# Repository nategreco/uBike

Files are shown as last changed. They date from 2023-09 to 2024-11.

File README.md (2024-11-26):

# Universal Bike Controller
The Universal Bike Controller is an open-source project aimed at providing a drop-in replacement for the factory console on NordicTrack® S-series exercise bikes (s10i, s15i, s22i, and s27i). This project allows you to upgrade and customize your bike's control system with new features and improvements.

## Explanation
The factory consoles on NordicTrack® S-series bikes may lack certain features or customization options that users desire. The Universal Bike Controller project addresses these limitations by providing an open-source solution that simplifies the hardware on the bike while unlocking connectivity to other third-party apps (Zwift®, Rouvy®, Peloton®) and smart devices.

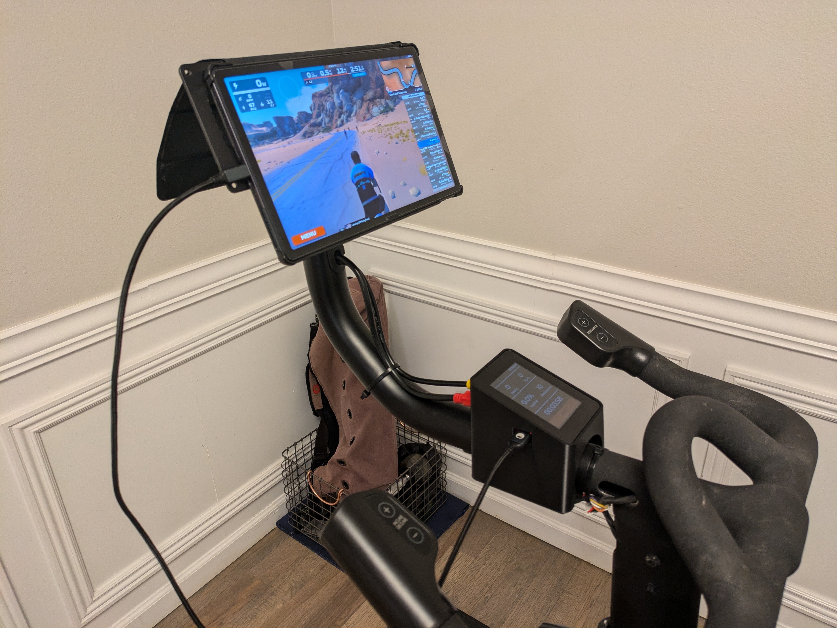
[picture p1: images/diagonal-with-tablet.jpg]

(Tablet not included)

## Features
- Drop-in replacement controller for the iFit console
  - **Note - This controller and the OEM console cannot be used together**
- Full incline and resistance control via OEM handlebar pushbuttons
- Wireless connectivity to a variety of third-party applications
- 3.5" TFT touchscreen for reseting elapsed time
- USB Type A fast charger port for charging
- Over-the-air support for future software upgrades

## Installation
The replacement uBike console mounts in the current location of the weight tray and plugs into the same two cables as the factory console. Installation is as simple as follows:
1. Turn off the bike
1. Remove the 4 screws from the underside of the weight tray (save them) and remove the weight tray
1. Place the uBike controller in its place, with the connectors facing away from the rider
1. Use the same 4 screws removed from the weight tray to secure the uBike controller
1. Unplug the 2 cables from the factory console and plug them into the new uBike controller
  * **Please see note below on compatability if you do not have a red and yellow connector**

## Compatibility
The Universal Bike Controller is designed to be compatible with the following NordicTrack® S-series exercise bikes:
- s10i
- s15i
- s22i
- s27i

All of these versions have been tested and are working.  Additionally, since 2021 bikes have stopped shipping with the yellow and red mini-DIN connectors to the console, instead they have cables coming directly out of the console.  **If your bike does not have the red and yellow connectors** you will need to buy the cables below:
* Yellow mini-DIN-6 Connector - PN 411540 ([eBay](https://www.ebay.com/itm/255061719835)/[HydraFitness](https://hydrafitnessparts.com/collections/stationary-bike-wires-and-wire-harness/products/nordictrack-comm-s22i-s15i-s10i-stationary-bike-upper-wire-harness-411540))
* Red mini-DIN-8 Connector - PN 411536 ([eBay](https://www.ebay.com/itm/265237954787)/[HydraFitness](https://hydrafitnessparts.com/collections/stationary-bike-wires-and-wire-harness/products/nordictrack-comm-s22i-s15i-s10i-stationary-bike-extension-wire-harness-4115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))

## Additional Reference Photos
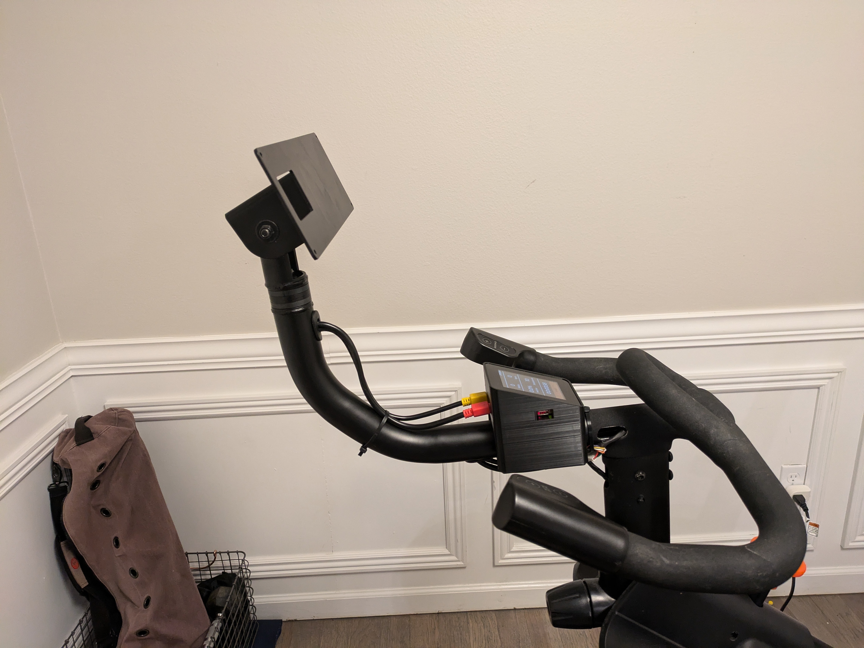
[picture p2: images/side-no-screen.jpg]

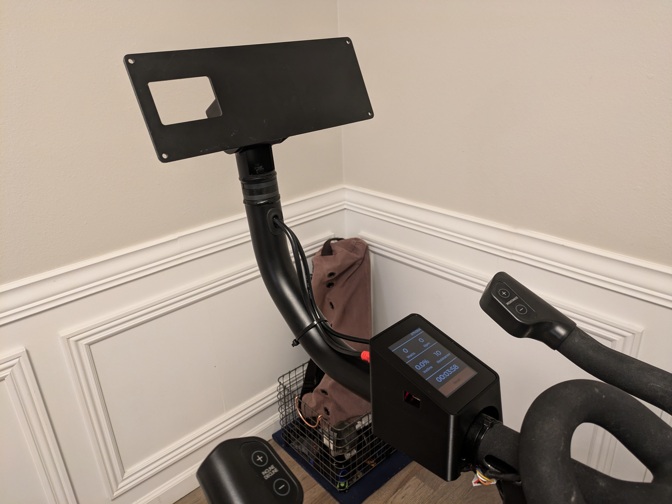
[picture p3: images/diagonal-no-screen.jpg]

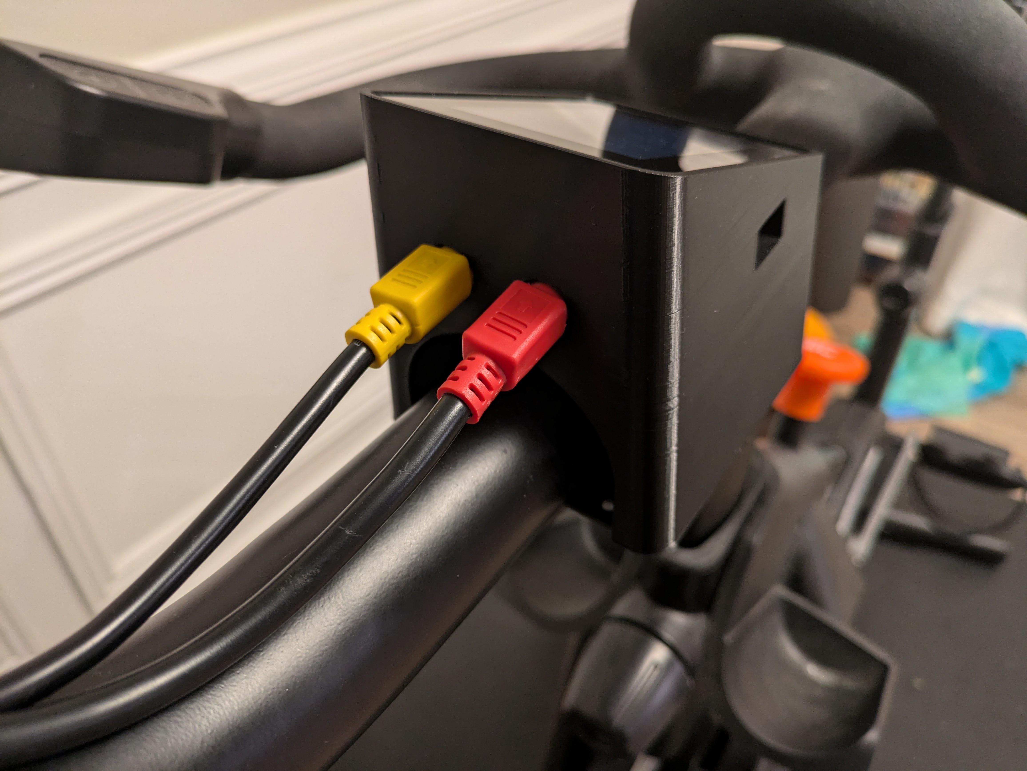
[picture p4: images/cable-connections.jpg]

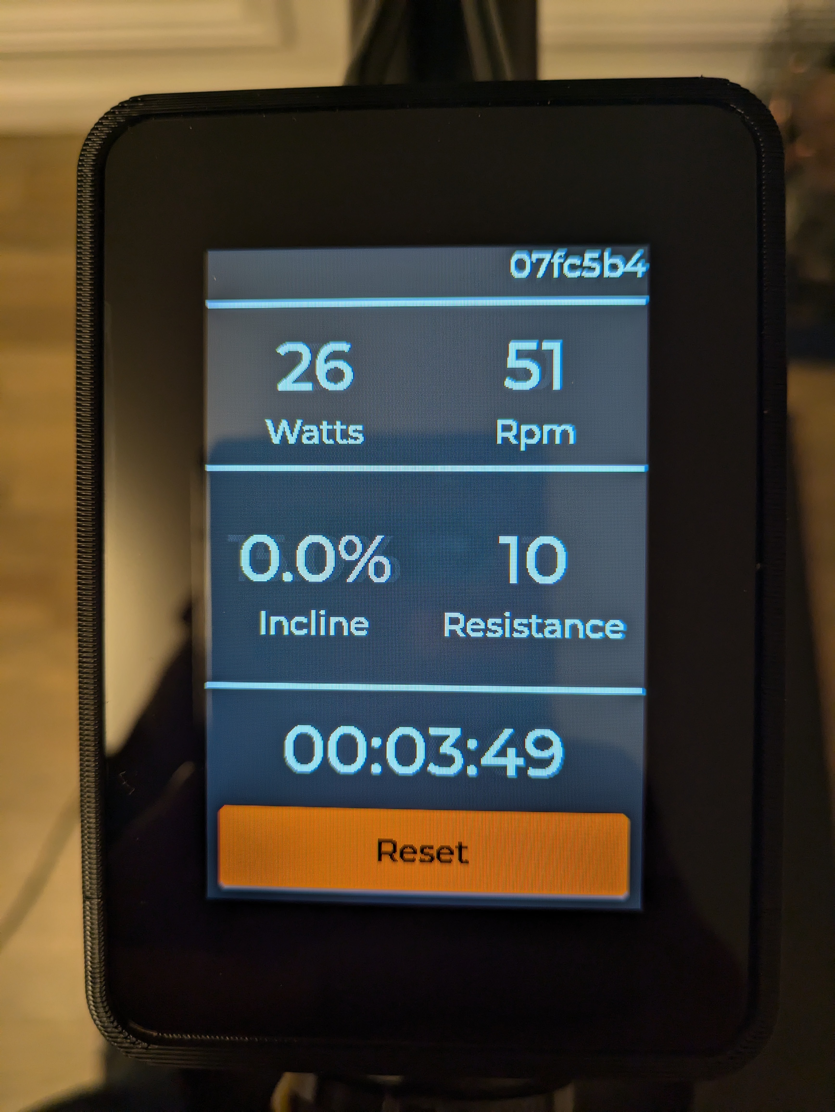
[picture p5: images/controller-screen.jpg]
Universal Bike Controller

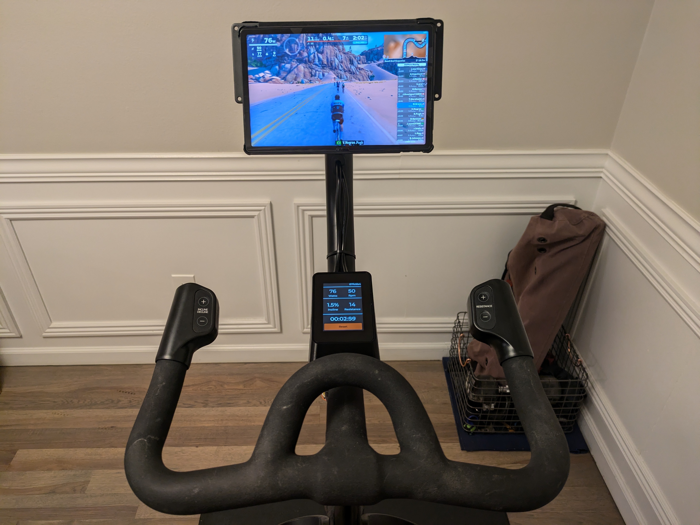
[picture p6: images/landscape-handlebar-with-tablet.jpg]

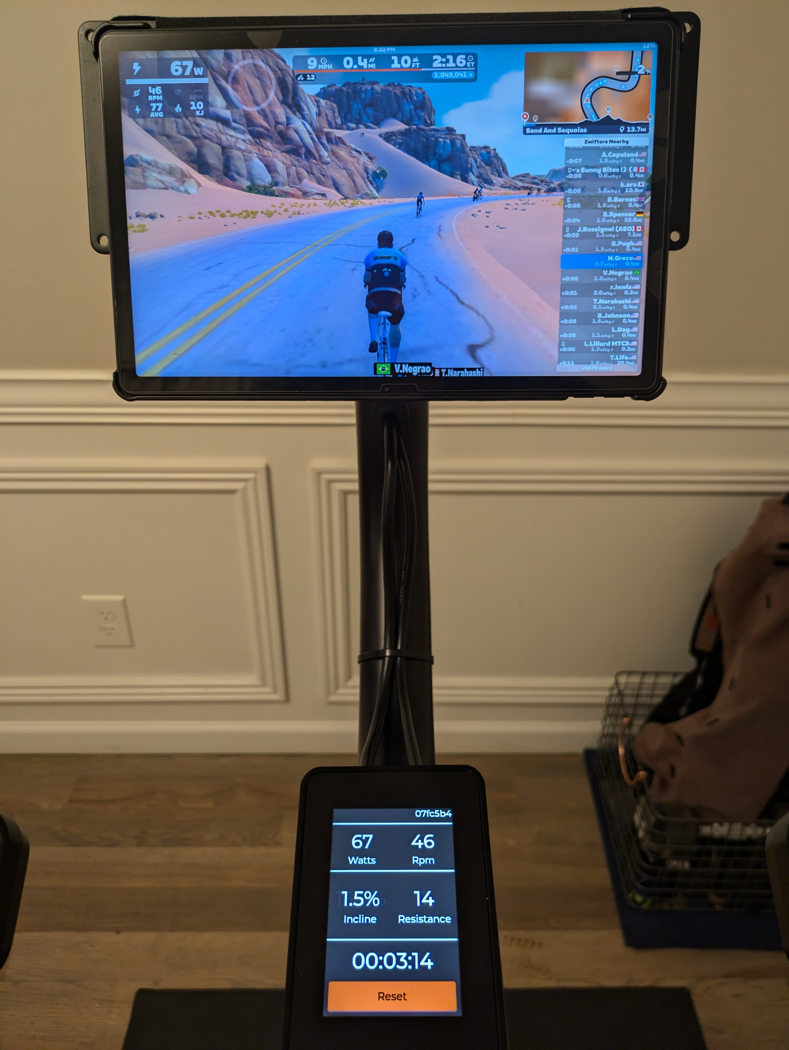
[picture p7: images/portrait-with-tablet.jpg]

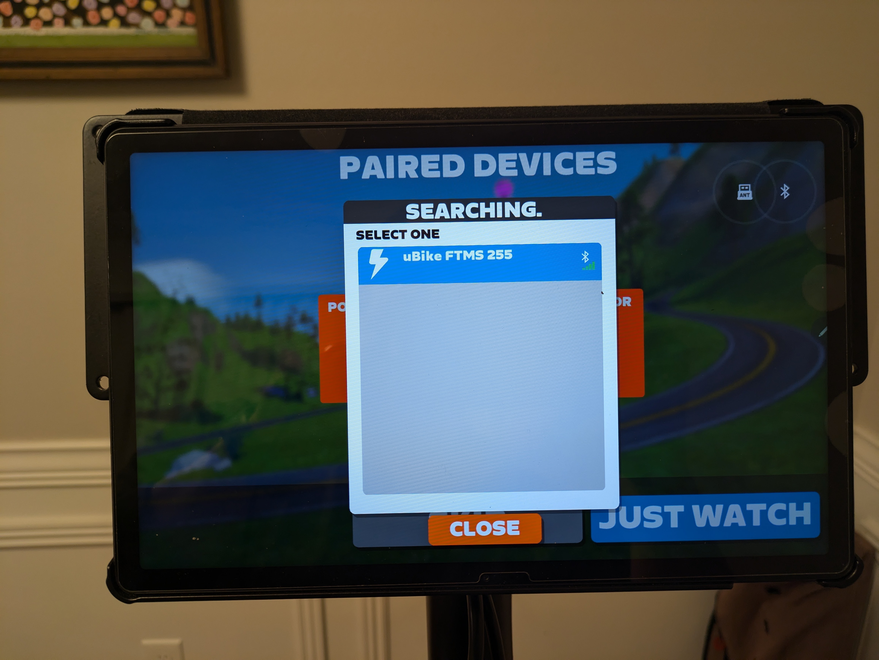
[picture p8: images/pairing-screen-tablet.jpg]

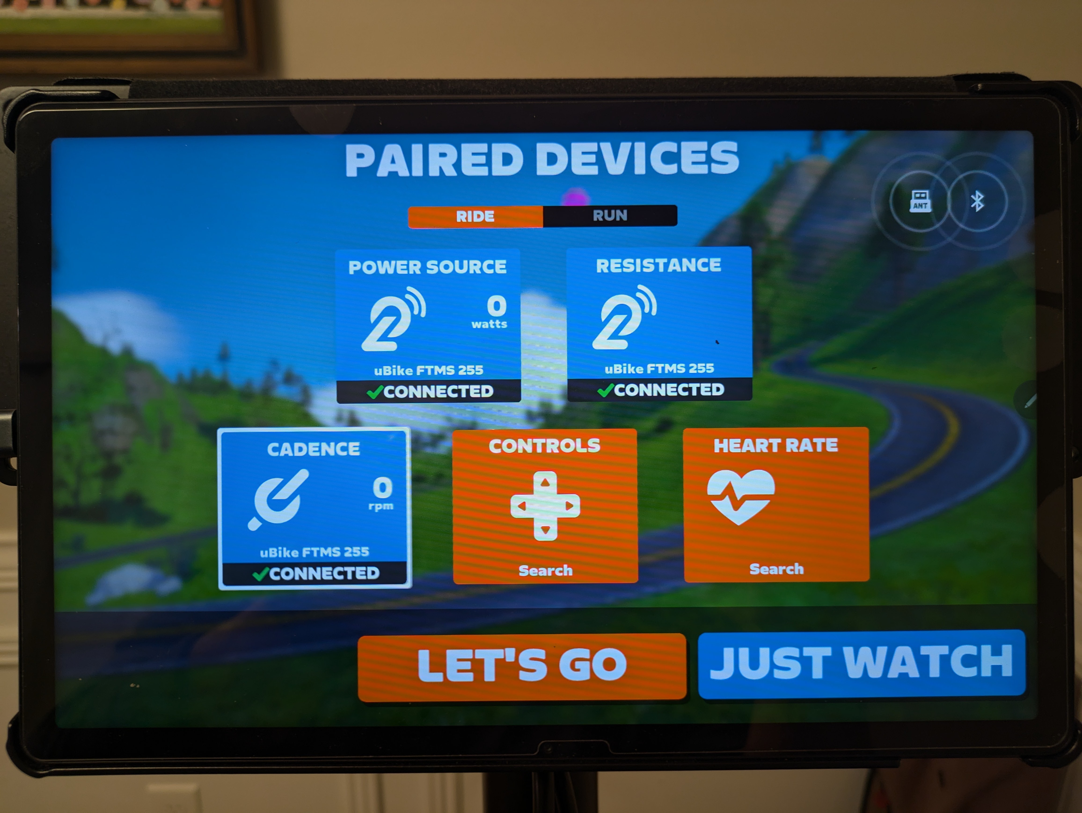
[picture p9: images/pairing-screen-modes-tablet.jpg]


## Development
Contributing to the project is encouraged and can be done by testing and reporting issues or software/hardware development.

### Hardware Overview
The hardware is composed of the following components:
* Controller PCB board
* [4D LCD 3.5" Capacitive Touch TFT-LCD](https://4dsystems.com.au/products/4dlcd-35480320-ctp-clb-ips/) 
* Controller enclosure
* Base mount for the enclosure

### Software Tools
* FreeCAD - Housing modeling
* KiCad - PCB Design
* nRF Connect 2.3.0 w/ Visual Studio Code extension - Firmware Development
* Python - Misc development and testing scripts

### Building Firmware
* Open folder `firmware/zephyr-project` in VS Code
* Open nRF Connect extension and press 'Create Build Configuration'
* Select 'ubike_v03' board
* Use defaults and press 'Build Configuration'
* Should produce a binary in `firmware/zephyr-project/build/zephyr/zephyr.hex`

### Flashing
* Open nRF Connect Programmer
* Press 'Add file' and select `firmware/zephyr-project/build/zephyr/zephyr.hex`
* Connect a [nRF52840 DK development board](https://www.nordicsemi.com/Products/Development-hardware/nRF52840-DK) or other SWD/JTAG programmer
* Select the development board as programming device
* Press 'Erase & write'

## Authors
* [@nategreco](https://github.com/nategreco)

## Need Hardware?
[Check out our store on Tindie](https://www.tindie.com/products/grecoengineer/universal-bike-controller/)

**Disclaimer**: This project is not affiliated with or endorsed by ICON Health Fitness, Inc (Nordictrack®) or its parent company. Use this software at your own risk, and be aware that modifying your exercise bike may void any warranties.

---

Contributions, feedback, and bug reports are welcome. Feel free to fork, contribute, or open issues to improve the Universal Bike Controller project!

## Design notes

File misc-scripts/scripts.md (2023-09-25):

# Misc Scripts
A few scripts that were used to reverse engineer the bike:
* serial-test.py
  * A script for sniffing the RS-485 comms
* sim-bike.py
  * A script that simulates the bike for building a table of wattage based on a given cadence and resistance
* create-data.py
  * A script for building additional wattage data beyond what was manually collected
* curve-fit.py
  * A script to curve-fit a polynomial to the wattage data

The wattage calculation relies on curve-fit data manually collected from the console when simulating an input cadence. Because of the spareness of the data, additional 'fake' data was produced for input to the curve fitting.

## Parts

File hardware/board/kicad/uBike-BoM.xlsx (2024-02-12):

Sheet: BOM
 |  |  | uBike v0.4 Bill of Materials
Item # | *Designator | *Qty | Manufacturer | *Mfg Part # | Description / Value | *Package/Footprint | Type | Your Instructions / Notes
1 | C1, C3, C9 | 3 | AVX | 08053C104KAT2A | 100nF - Unpolarized capacitor, 25V, 10% | 0805_2012Metric
2 | C2 | 1 | Panasonic | 20SVPF120M | 120uF - Organic Polymer Capacitors 20V, ESR 25mohm | 20SVPF120M
3 | C4, C8 | 2 | Murata Electronics | GRM319R61E106MA12D | 10uF - Unpolarized capacitor, 25V, 10% | 1206_3216Metric
4 | C5, C6 | 2 | Kemet | C0603C120F5GACTU | 12pF - Unpolarized capacitor, 50V, 1% | 0603_1608Metric
5 | C7 | 1 | Chemi-Con | EMVY630ARA221MKE0S | 220uF - Electrolytic Capacitor, 63 Volt | EMVY630ARA221MKE0S
6 | C10 | 1 | Murata Electronics | GRT21BR61E105KE13L | 1uF - Unpolarized capacitor, 25V, 10% | 0805_2012Metric
7 | D1, D4, D6 | 3 | Bourns | CDSOT23-SM712 | Surface Mount Bi-directional TVS Diode | SOT-23
8 | D2 | 1 | Lite-On | LTST-C150KGKT | Light emitting diode (Green) | 1206_3216Metric
9 | D3 | 1 | Lite-On | LTST-C150KRKT | Light emitting diode (Red) | 1206_3216Metric
10 | D5 | 1 | Onsemi | SS24FL | Schottky Diodes & Rectifiers 40V, 2A SCHOTTKY | SS24FL
11 | F1 | 1 | Littelfuse, Inc | 1206L200SLYR | 2A Resettable Fuse | 1206_3216Metric
12 | H1, H2, H3, H4 | 4 | - | - | Mounting Hole without connection | - |  | DO NOT POPULATE
13 | J1 | 1 | Kycon, Inc. | KMDGX-6S-BS | 6P mini-DIN connector female (socket) | KMDGX6SBS
14 | J2 | 1 | Amphenol ICC | F31S-1A7L1-11040 | 40P FPC connector | F31S1A7L111040
15 | J3 | 1 | Kycon, Inc. | KMDGX-8S-BS | 8P mini-DIN connector female (socket) | KMDGX8SBS
16 | J4 | 1 | - | - | 10P Tag Connect footprint (DNP) | - |  | DO NOT POPULATE
17 | J5 | 1 | Amphenol ICC | 87520-0010BLF | USB Type A, Standard, Right Angle, Through Hole | 875200010BLF
18 | L1 | 1 | Coilcraft | MSS1210-683MED | Power Inductors 68uH Shld 20% 4.3A 84mOhms | MSS1210-683MED
19 | Q1 | 1 | Diotec Semiconductor | MMBT3904 | Bipolar NPN Transistor | SOT-23
20 | R1, R2, R3, R6, R7, R8, R20 | 7 | Panasonic | ERJ-P06F68R0V | Thick Film Resistor – 68 (1/2W) | 0805_2012Metric
21 | R4 | 1 | Panasonic | ERJ-PA3F1002V | Thick Film Resistor – 10k (1/4W) | 0603_1608Metric
22 | R9, R10 | 2 | Panasonic | ERJ-PA3F1691V | Thick Film Resistor – 1.69k (1/4W) | 0603_1608Metric
23 | R11 | 1 | Panasonic | ERJ-PA3F1001V | Thick Film Resistor – 1k (1/4W) | 0603_1608Metric
24 | R13 | 1 | Panasonic | ERJ-PA3F2200V | Thick Film Resistor – 220 (1/4W) | 0603_1608Metric
25 | R14, R15, R21, R22, R23, R24 | 6 | Panasonic | ERJ-PA3F10R0V | Thick Film Resistor – 10 (1/4W) | 0603_1608Metric
26 | R18 | 1 | Panasonic | ERJ-PA3F3300V | Thick Film Resistor – 330 (1/2W) | 0805_2012Metric
27 | R19 | 1 | Panasonic | ERJ-PA3F1500V | Thick Film Resistor – 150 (1/4W) | 0603_1608Metric
28 | U1 | 1 | Texas Instruments | SN65HVD08DR | Wide Supply Range RS-485 Transceiver | SOIC127P600X175-8N
29 | U2 | 1 | STMicroelectronics | LD1117S33TR | 3.3v Fixed Low Drop Positive Voltage Regulator | SOT-223-3
30 | U3 | 1 | Raytac Corporation | MDBT50Q-1MV2 | Nordic nRF52840 SoC Solution | MDBT50Q
31 | U4 | 1 | Texas Instruments | LM2596SX-5.0/NOPB | Switching Voltage Regulators 150 KHZ 3A Buck | TO-263-5
32 | X1 | 1 | NDK | NX3215SA-32.768K-STD-MUA-9 | Crystal oscillator - 32.768 kHz | 1206
Need a quick and accurante quote? Need an efficient production? Please read SMT Ordering Necessary Files & Info in 1 minute. Thank you very much! (https://www.pcbway.com/smt_ordering_guide.html)
Click for Instructions on How to Create a BOM (https://www.pcbway.com/blog/PCB_Assembly/How_to_Build_a_BOM__Bill_Of_Materials_.html)

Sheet: KiCAD Output
Source: | C:\Users\natha\Projects\uBike\hardware\board\kicad\uBike.kicad_sch
Date: | 2024-02-11 17:42
Tool: | Eeschema 7.0.9
Generator: | C:\Program Files\KiCad\7.0\bin\scripting\plugins/bom_csv_grouped_by_value_with_fp.py
Component Count: | 53
Ref | Qnty | Value | Cmp name | Footprint | Description | Vendor | DNP
C1, C3, C9 | 3 | 100n | C | Capacitor_SMD:C_0805_2012Metric | Unpolarized capacitor
C2 | 1 | 120u | 20SVPF120M | libs:16SVF180M | Panasonic 120uF 20 V Polymer Aluminium Electrolytic Capacitor C6, OS-CON Series 5000h 6.3 x 5.9mm
C4, C8 | 2 | 10u | C | Capacitor_SMD:C_1206_3216Metric | Unpolarized capacitor
C5, C6 | 2 | 12p | C | Capacitor_SMD:C_0603_1608Metric | Unpolarized capacitor
C7 | 1 | 220u | EMVY630ARA221MKE0S | libs:CHEMI-KE0
C10 | 1 | 1u | C | Capacitor_SMD:C_0805_2012Metric | Unpolarized capacitor
D1, D4, D6 | 3 | CDSOT23-SM712 | CDSOT23-SM712 | libs:SOT95P230X117-3N | TVS Diode Dual Bi-Dir 7/12V 30KV SOT23 Bourns CDSOT23-SM712 Dual Bi-Directional TVS Diode, 400W peak, 3-Pin SOT-23
D2 | 1 | GREEN | LED | Diode_SMD:D_1206_3216Metric | Light emitting diode
D3 | 1 | RED | LED | Diode_SMD:D_1206_3216Metric | Light emitting diode
D5 | 1 | SS24FL | SS24FL | libs:SODFL3617X108N | ON SEMICONDUCTOR - SS24FL - SCHOTTKY RECT, AEC-Q101, 40V, SOD-123F
F1 | 1 | 2A | Polyfuse_Small | Diode_SMD:D_1206_3216Metric | Resettable fuse, polymeric positive temperature coefficient, small symbol
H1, H2, H3, H4 | 4 | MountingHole | MountingHole | MountingHole:MountingHole_3.2mm_M3 | Mounting Hole without connection
J1 | 1 | KMDGX-6S-BS | KMDGX-6S-BS | libs:KMDGX6SBS | Circular DIN Connectors 6P R/A FULL SHIELD GOLD PLANTED
J2 | 1 | F31S-1A7L1-11040 | F31S-1A7L1-11040 | libs:F31S1A7L111040 | FFC & FPC Connectors F31S-1A7L1-11040-Flip type
J3 | 1 | KMDGX-8S-BS | KMDGX-8S-BS | libs:KMDGX8SBS | Circular DIN Connectors 8P R/A FULL SHIELD GOLD PLATED
J4 | 1 | TC2050-IDC-NL | TC2050-IDC-NL | Connector:Tag-Connect_TC2050-IDC-NL_2x05_P1.27mm_Vertical
J5 | 1 | 87520-0010BLF | 87520-0010BLF | libs:87520-0010BLF | USB 2.0, Input Output Connector, USB Type A, Standard, Right Angle, Through Hole, Single Decks, 4 Positions
L1 | 1 | MSS1210-683MED | MSS1210-683MED | libs:INDPM120120X1020N | COILCRAFT - MSS1210-683MED - INDUCTOR, 68UH, 4.3A, 20%, PWR, 4.5MHZ
Q1 | 1 | MMBT3904 | MMBT3904 | Package_TO_SOT_SMD:SOT-23 | 0.2A Ic, 40V Vce, Small Signal NPN Transistor, SOT-23
R1, R2, R3, R6, R7, R8, R20 | 7 | 68 | R | Resistor_SMD:R_0805_2012Metric | Resistor
R4 | 1 | 10k | R | Resistor_SMD:R_0603_1608Metric | Resistor
R9, R10 | 2 | 1k69 | R | Resistor_SMD:R_0603_1608Metric | Resistor
R11 | 1 | 1k | R | Resistor_SMD:R_0603_1608Metric | Resistor
R13 | 1 | 250 | R | Resistor_SMD:R_0603_1608Metric | Resistor
R14, R15, R21, R22, R23, R24 | 6 | 10 | R | Resistor_SMD:R_0603_1608Metric | Resistor
R18 | 1 | 330 | R | Resistor_SMD:R_0805_2012Metric | Resistor
R19 | 1 | 150 | R | Resistor_SMD:R_0603_1608Metric | Resistor
U1 | 1 | SN65HVD08DR | SN65HVD08DR | libs:SOIC127P600X175-8N | TEXAS INSTRUMENTS - SN65HVD08DR - Transceiver, RS485, 1 Driver, 3 V to 5.5 V Supply, SOIC-8
U2 | 1 | LD1117S33TR_SOT223 | LD1117S33TR_SOT223 | Package_TO_SOT_SMD:SOT-223-3_TabPin2 | 800mA Fixed Low Drop Positive Voltage Regulator, Fixed Output 3.3V, SOT-223
U3 | 1 | MDBT50Q-P1MV2 | MDBT50Q-P1MV2 | RF_Module:Raytac_MDBT50Q | Multiprotocol BLE/ANT/2.4 GHz/802.15.4 Cortex-M4F SoC, nRF52840 module
U4 | 1 | LM2596S-5 | LM2596S-5 | Package_TO_SOT_SMD:TO-263-5_TabPin3 | 5V 3A Step-Down Voltage Regulator, TO-263
X1 | 1 | 32.768kHz | Crystal | Resistor_SMD:R_1206_3216Metric | Two pin crystal

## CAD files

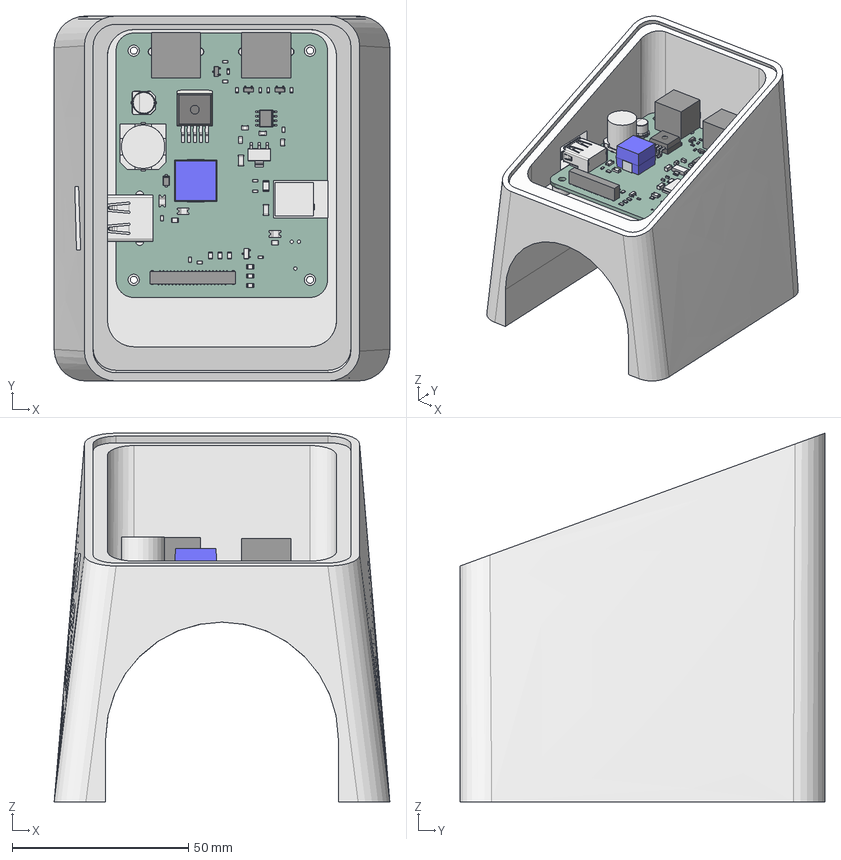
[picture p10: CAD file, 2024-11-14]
hardware/models/freecad/uBike-v4.FCStd
95.2 x 103.6 x 104.6 mm
uBike PCB

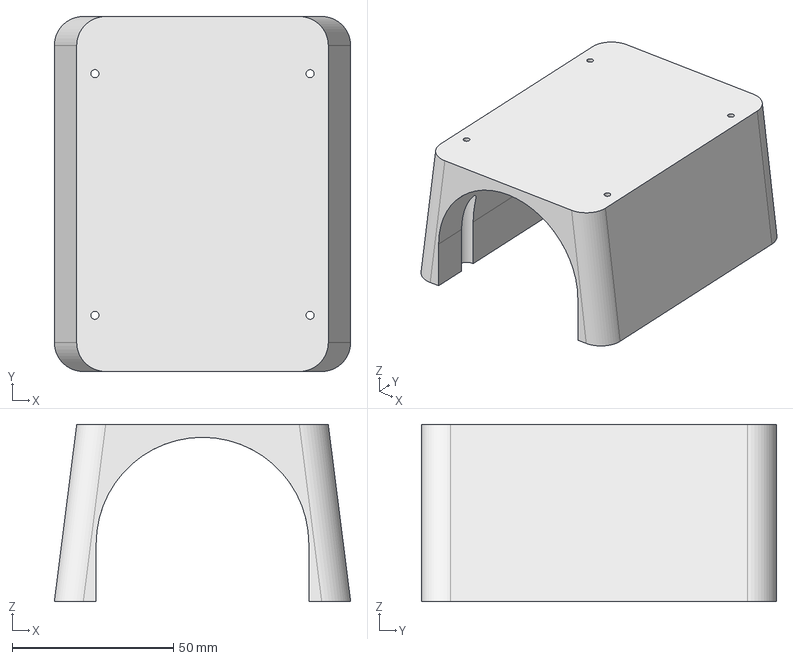
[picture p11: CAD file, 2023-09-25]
hardware/models/freecad/uBikeBase.FCStd
92.0 x 110.2 x 55.0 mm

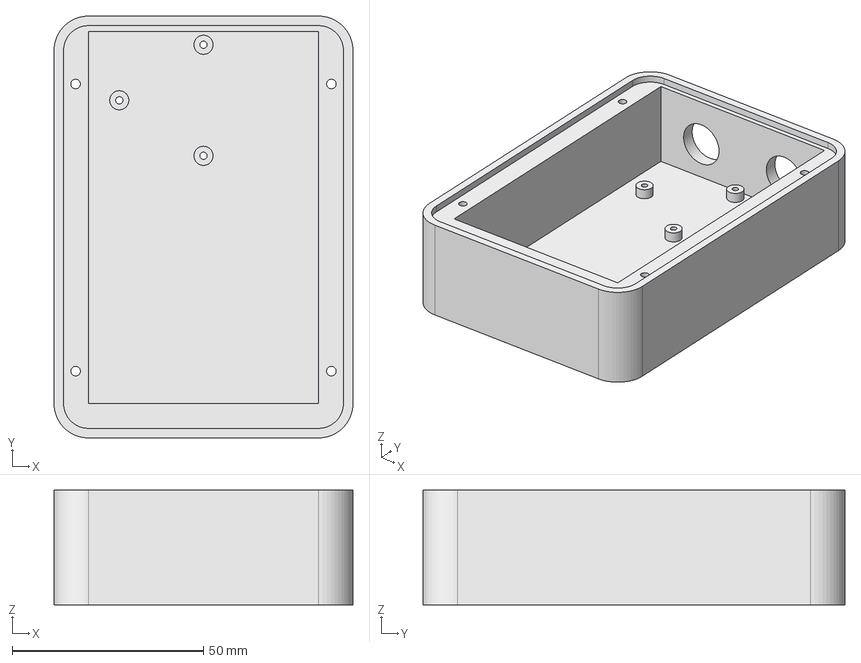
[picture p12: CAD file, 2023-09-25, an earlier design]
hardware/models/freecad/uBike.FCStd
78.1 x 110.2 x 30.0 mm

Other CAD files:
hardware/models/uBike-v4.stl

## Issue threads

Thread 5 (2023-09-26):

Redesign board

nategreco, 2023-09-26:
- nRF53 series (maybe?)
  - Multicore could help LCD be more responsive
- USB Charge port
  - Previously added a type A fast charge port but removed due to part procurement issues
- Rotate LCD 180 degrees
  - This allows some tilt of the board and easier connectivity
- TVS diodes for ESD protection
- Pi filter on incoming 12v
- Current protection in incoming 12v and outgoing 5v for USB
- 4 Layer board with dedicated ground/power planes
- Tag connect pogo pad for swd programming
- Volatile memory (for settings, last resistance, previously paired devices, etc)
- Larger mounting holes

nategreco, 2024-01-04:
See:
https://github.com/nategreco/uBike/tree/v3-board-design

Closed 2024-01-04.

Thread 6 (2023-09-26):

Redesign enclosure

nategreco, 2023-09-26:
Ideally:
- 1 piece
- Downward tilt of LCD

This should wait on board redesign

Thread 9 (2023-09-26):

Collect new power data and revise curve fit

nategreco, 2023-09-26:
Power data was way too sparse, should collected from 15 to 255 rpm also over the whole resistance range (0-255?).

Then the polynomial I'm using for curve fitting needs revised.  A 7th order polynomial surely isn't right, there must be a log function/exponential/etc in the NT 'force' calculation.

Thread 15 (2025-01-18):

Build doesn't support later toolchains

rjlee, 2025-01-18:
I've just tried to compile the firmware using the instructions in the readme. After some trial and error, I've managed to compile it using the 2.3.0 SDK toolchain.

The 2.4.0 and later (up to the latest 2.9.0) fail with what looks to be this issue: https://devzone.nordicsemi.com/f/nordic-q-a/102974/mcuboot_smp_ble-west-build-failed

Log:
```
C:/Users/robl/Projects/uBike/firmware/zephyr-project/prj.conf:20: warning: attempt to assign the value 'y' to the undefined symbol COUNTER_RTC2
C:/Users/robl/Projects/uBike/firmware/zephyr-project/prj.conf:45: warning: attempt to assign the value '8' to the undefined symbol LV_Z_MEM_POOL_NUMBER_BLOCKS
C:/Users/robl/Projects/uBike/firmware/zephyr-project/prj.conf:55: warning: attempt to assign the value 'y' to the undefined symbol LV_Z_POINTER_KSCAN
C:/Users/robl/Projects/uBike/firmware/zephyr-project/prj.conf:60: warning: attempt to assign the value 'y' to the undefined symbol KSCAN_FT5336
C:/Users/robl/Projects/uBike/firmware/zephyr-project/prj.conf:62: warning: attempt to assign the value 'y' to the undefined symbol KSCAN_FT5336_INTERRUPT
C:/Users/robl/Projects/uBike/firmware/zephyr-project/prj.conf:64: warning: attempt to assign the value 'y' to the undefined symbol LV_Z_POINTER_KSCAN_SWAP_XY
C:/Users/robl/Projects/uBike/firmware/zephyr-project/prj.conf:65: warning: attempt to assign the value 'y' to the undefined symbol LV_Z_POINTER_KSCAN_INVERT_Y
C:/Users/robl/Projects/uBike/firmware/zephyr-project/prj.conf:75: warning: attempt to assign the value 'y' to the undefined symbol MCUMGR_CMD_IMG_MGMT
C:/Users/robl/Projects/uBike/firmware/zephyr-project/prj.conf:76: warning: attempt to assign the value 'y' to the undefined symbol MCUMGR_CMD_OS_MGMT
C:/Users/robl/Projects/uBike/firmware/zephyr-project/prj.conf:80: warning: attempt to assign the value 'y' to the undefined symbol MCUMGR_SMP_BT
C:/Users/robl/Projects/uBike/firmware/zephyr-project/prj.conf:81: warning: attempt to assign the value 'n' to the undefined symbol MCUMGR_SMP_BT_AUTHEN

error: Aborting due to Kconfig warnings
```

Also, the instructions say use the `'ubike_v03` board, but there is a v04 as well - which is the one used by the tindie distributed boards ?

I guess this a a feature request to update the project build files to support the latest toolchain and also clarification on which board configuration to use.

rjlee, 2025-01-18:
It would also be good to know what SDK version you are using as well, just so I can have the same environment when building.

nategreco, 2025-01-18:
Hey @rjlee - Welcome to the project!  I think yourself and one other have expressed interest in the project, I need to clean up these tickets. I'll try and do that this weekend.

To answer a few questions, I initially started updating to the latest Nordic/Zephyr SDK, and boy has a lot changed. I am not sure it's worth pursuing, I forget what I even wanted from it but I remember there were tons of configurations changes across the major versions that made it a bit ugly. If you want to pursue it though I'd be excited.

Regarding board revisions I have shipped V4 but there were no device tree changes V3 to V4 so code still references V3. V4 mostly added the switching regulator and USB charging port.

nategreco, 2025-01-18:
I lied - v4 was a different device tree. I still have some v3s around so I kept the dts stuff in the repo.  It can be axed at this point.

nategreco, 2025-01-18:
I confirmed I am using the 2.3.0 toolchain. looks like newest is 2.6.2.

rjlee, 2025-01-19:
Thanks for letting me know that it's 2.3.0 - from my experiments, that's the only version of the toolchain that it compiles with.  It looks like the newest is 2.9.0, that's what my vscode offers - https://github.com/nrfconnect/sdk-nrf/releases.

I've purchased a nRF52840 dongle to experiment with, just waiting for it to arrive, so will try flashing to that and using it as a bit of a dev board.

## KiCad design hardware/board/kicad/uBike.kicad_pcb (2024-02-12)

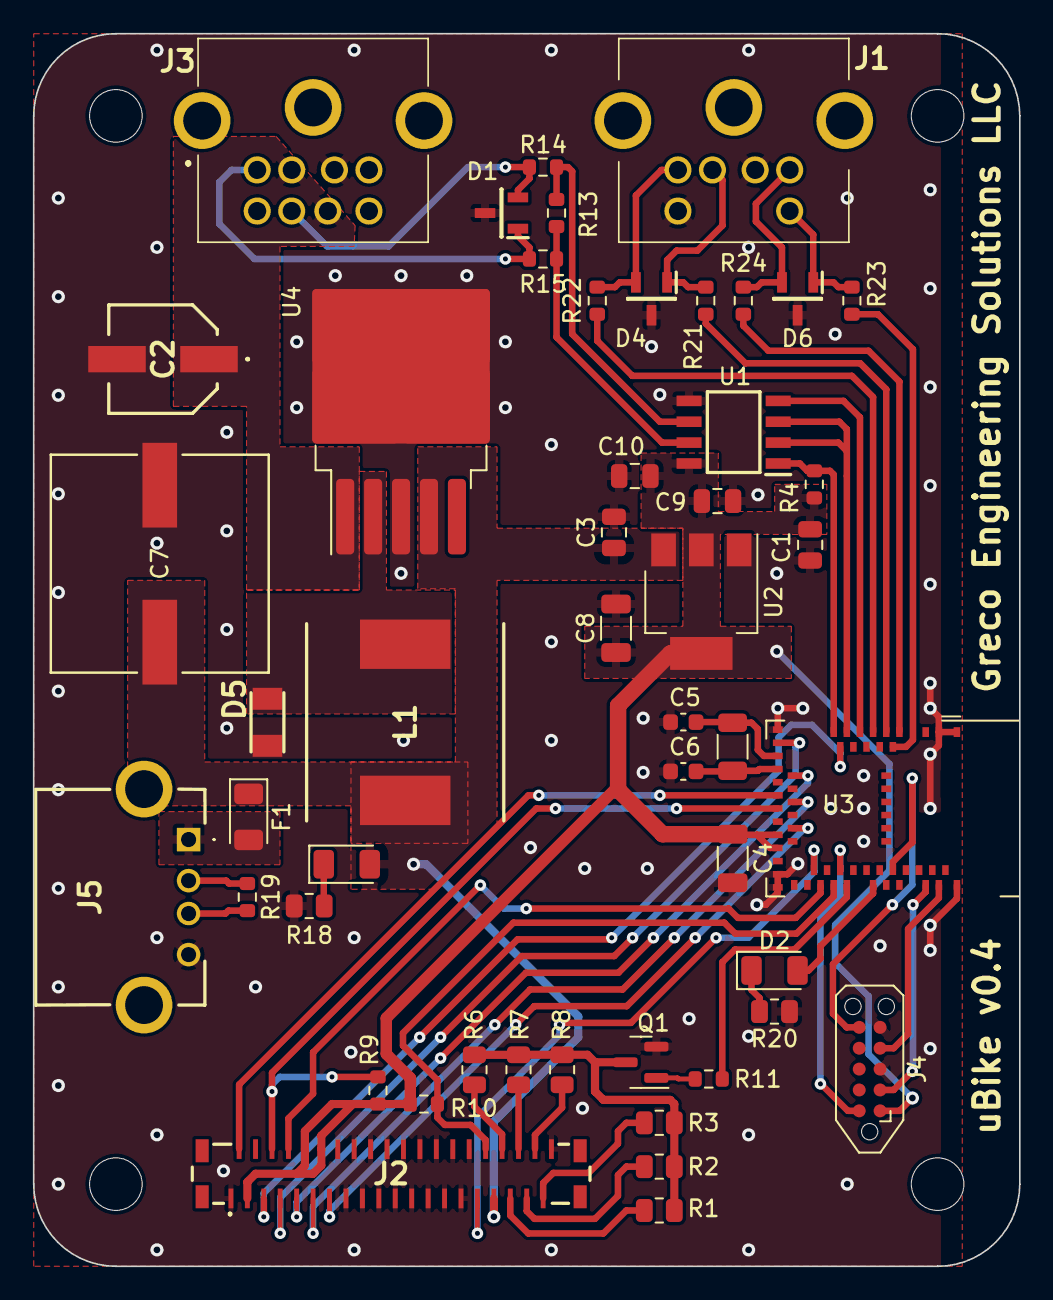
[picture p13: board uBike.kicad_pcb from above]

Board: 2 copper layers, 60.0 x 75.0 mm, 53 parts (0 on the bottom side), 51 nets.

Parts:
C1, C3, C9: 100n; C_0805_2012Metric
C2: 120u; 16SVF180M
C4, C8: 10u; C_1206_3216Metric
C5, C6: 12p; C_0603_1608Metric
C7: 220u; CHEMI-KE0
C10: 1u; C_0805_2012Metric
D1, D4, D6: CDSOT23-SM712; SOT95P230X117-3N
D2: GREEN; D_1206_3216Metric
D3: RED; D_1206_3216Metric
D5: SS24FL; SODFL3617X108N
F1: 2A; D_1206_3216Metric
H1, H2, H3, H4: MountingHole; MountingHole_3.2mm_M3
J1: KMDGX-6S-BS; KMDGX6SBS
J2: F31S-1A7L1-11040; F31S1A7L111040
J3: KMDGX-8S-BS; KMDGX8SBS
J4: TC2050-IDC-NL; Tag-Connect_TC2050-IDC-NL_2x05_P1.27mm_Vertical
J5: 87520-0010BLF
L1: MSS1210-683MED; INDPM120120X1020N
Q1: MMBT3904; SOT-23
R1, R2, R3, R6, R7, R8, R20: 68; R_0805_2012Metric
R4: 10k; R_0603_1608Metric
R9, R10: 1k69; R_0603_1608Metric
R11: 1k; R_0603_1608Metric
R13: 250; R_0603_1608Metric
R14, R15, R21, R22, R23, R24: 10; R_0603_1608Metric
R18: 330; R_0805_2012Metric
R19: 150; R_0603_1608Metric
U1: SN65HVD08DR; SOIC127P600X175-8N
U2: LD1117S33TR_SOT223; SOT-223-3_TabPin2
U3: MDBT50Q-P1MV2; Raytac_MDBT50Q
U4: LM2596S-5; TO-263-5_TabPin3
X1: 32.768kHz; R_1206_3216Metric

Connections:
+3.3V: C1.1, C4.1, C8.1, C9.2, C10.2, J2.3, J2.10, J2.12, J4.1, R4.1, R9.1, R10.1, U1.8 (VCC), U2.2 (VO), U3.28 (VDD), U3.30 (VDDH)
+5V: C3.1, C7.1, D3.2 (A), F1.1, J2.33, L1.2, U2.3 (VI), U4.4 (FB)
+12V: C2.1 (+), J3.1, J3.7, U4.1 (VIN)
BL_DRAIN: Q1.3 (C), R1.1, R2.1, R3.1, R6.2, R7.2, R8.2
BL_PWM: R11.1, U3.41 (P0.17)
CS: J2.9, U3.19 (P0.26)
CTP_SCL: J2.6, R9.2, U3.24 (P0.08)
CTP_SDA: J2.32, R10.2, U3.39 (P0.15)
DE: U1.2 (~RE), U1.3 (DE), U3.12 (P0.31/AIN7)
GND: C1.2, C2.2 (-), C3.2, C4.2, C5.2, C6.2, C7.2, C8.2, C9.1, C10.1, D1.3, D4.3, D5.2 (A), D6.3, J1.2, J1.6, J2.1, J2.14, J2.15, J2.16, J2.17, J2.18, J2.19, J2.20, J2.21, J2.22, J2.23, J2.24, J2.25, J2.26, J2.27, J2.28, J2.29, J2.30, J2.40, J3.2, J3.6, J4.3, J4.5, J5.4, Q1.2 (E), R18.1, R20.1, U1.5 (GND), U2.1 (GND), U3.1 (GND), U3.2 (GND), U3.15 (GND), U3.32 (VBUS), U3.33 (GND), U3.55 (GND), U4.3 (GND)
IN1: R21.1, U3.6 (P1.13)
IN2: R22.2, U3.8 (P1.15)
IN3: R24.2, U3.4 (P1.11)
IN4: R23.1, U3.5 (P1.12)
unnamed: D2.2 (A), U3.44 (P0.20)
unnamed: D2.1 (K), R20.2
unnamed: D3.1 (K), R18.2
unnamed: D4.1, J1.1, R21.2
unnamed: D4.2, J1.3, R22.1
unnamed: D5.1 (K), L1.1, U4.2 (OUT)
unnamed: D6.1, J1.8, R23.2
unnamed: D6.2, J1.5, R24.1
unnamed: F1.2, J5.1
unnamed: J2.34, R6.1
unnamed: J2.35, R1.2
unnamed: J2.36, R7.1
unnamed: J2.37, R2.2
unnamed: J2.38, R8.1
unnamed: J2.39, R3.2
unnamed: J5.2, R19.1
unnamed: J5.3, R19.2
unnamed: Q1.1 (B), R11.2
unnamed: R13.2, R14.2, U1.6 (A)
unnamed: R13.1, R15.2, U1.7 (B)
unnamed: C5.1, U3.17 (XL1/P0.00), X1.2
unnamed: C6.1, U3.18 (XL2/P0.01), X1.1
RESET: J2.7, U3.16 (P0.27)
RS: J2.8, U3.37 (P0.13)
RS485_A: D1.2, J3.4, R14.1
RS485_B: D1.1, J3.3, R15.1
RX: R4.2, U1.1 (R), U3.14 (P0.30/AIN6)
SCL: J2.11, U3.23 (TRACECLK/P0.07)
SDI: J2.2, U3.22 (P0.06)
SDO: J2.13, U3.27 (TRACEDATA2/P0.11)
SWCLK: J4.4, U3.53 (SWDCLK)
SWDIO: J4.2, U3.51 (SWDIO)
SWD_RST: J4.10, U3.40 (~RESET/P0.18)
SWO: J4.6, U3.47 (TRACEDATA0/P1.00)
TX: U1.4 (D), U3.10 (P0.29/AIN5)
YD: J2.5, U3.13 (P0.28/AIN4)
YU: J2.31, U3.36 (P0.14)

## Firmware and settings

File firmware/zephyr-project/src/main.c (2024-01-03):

/*
 * Universal Bike Controller
 * Copyright (C) 2022-2023, Greco Engineering Solutions LLC
 *
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
 * You should have received a copy of the GNU General Public License
 * along with this program.  If not, see <http://www.gnu.org/licenses/>.
 */

#include <stdio.h>
#include <stdlib.h>
#include <string.h>
#include <zephyr/bluetooth/bluetooth.h>
#include <zephyr/bluetooth/conn.h>
#include <zephyr/bluetooth/gatt.h>
#include <zephyr/bluetooth/uuid.h>
#include <zephyr/drivers/counter.h>
#include <zephyr/drivers/gpio.h>
#include <zephyr/drivers/uart.h>
#include <zephyr/kernel.h>
#include <zephyr/logging/log.h>
#include <zephyr/mgmt/mcumgr/transport/smp_bt.h>
#include <zephyr/random/rand32.h>
#include <zephyr/types.h>

#include "asciiModbus.h"
#include "bikeControl.h"
#include "cps.h"
#include "cscs.h"
#include "display.h"
// #include "fec.h"
#include "ftms.h"
#include "version.h"

LOG_MODULE_REGISTER ( app );

#define DEVICE_NAME CONFIG_BT_DEVICE_NAME
#define DEVICE_NAME_LEN ( sizeof ( DEVICE_NAME ) - 1 )
#define BT_DEVICE_CYCLING_APPEARANCE 0x012

#define TGT_CYCLE_MS 500

#define LED0_NODE DT_ALIAS ( led0 )
#define RS485DE_NODE DT_ALIAS ( rs485de )
#define CPT_RST_NODE DT_ALIAS ( cptrst )

#define BUT1_NODE DT_ALIAS ( addinc )
#define BUT2_NODE DT_ALIAS ( subinc )
#define BUT3_NODE DT_ALIAS ( addres )
#define BUT4_NODE DT_ALIAS ( subres )

#define INC_ALARM_ID 0
#define RES_ALARM_ID 1

#define RX_BUFF_SIZE 100
#define TX_BUFF_SIZE 20
#define RX_TIMEOUT_US 2000
#define TX_TIMEOUT_US 2000
#define SEM_TIMEOUT K_MSEC ( 50 )

static const struct bt_data ad []
    = { BT_DATA_BYTES ( BT_DATA_GAP_APPEARANCE,
                        ( BT_DEVICE_CYCLING_APPEARANCE >> 0 ) & 0xff,
                        ( BT_DEVICE_CYCLING_APPEARANCE >> 8 ) & 0xff ),
        BT_DATA_BYTES ( BT_DATA_FLAGS,
                        ( BT_LE_AD_GENERAL | BT_LE_AD_NO_BREDR ) ),
        BT_DATA_BYTES ( BT_DATA_UUID16_ALL,
                        BT_UUID_16_ENCODE ( BT_UUID_CPS_VAL ),
                        BT_UUID_16_ENCODE ( BT_UUID_CSC_VAL ),
                        BT_UUID_16_ENCODE ( BT_UUID_FTMS_VAL ) ),
        BT_DATA ( BT_DATA_NAME_COMPLETE, DEVICE_NAME, DEVICE_NAME_LEN ) };

static const struct bt_data sd [] = {
    BT_DATA_BYTES ( BT_DATA_UUID128_ALL,
                    0x84,
                    0xaa,
                    0x60,
                    0x74,
                    0x52,
                    0x8a,
                    0x8b,
                    0x86,
                    0xd3,
                    0x4c,
                    0xb7,
                    0x1d,
                    0x1d,
                    0xdc,
                    0x53,
                    0x8d ),
};

static void adv_start ( void )
{
    int err;

    err = bt_le_adv_start ( BT_LE_ADV_CONN,
                            ad,
                            ARRAY_SIZE ( ad ),
                            sd,
                            ARRAY_SIZE ( sd ) );
    if ( err ) {
        LOG_ERR ( "Advertising failed to start (err %d)", err );
        return;
    }

    LOG_INF ( "Advertising successfully started" );
}

static void connected ( struct bt_conn *conn, uint8_t err )
{
    if ( err ) {
        LOG_ERR ( "Connection failed (err 0x%02x)", err );
    } else {
        LOG_INF ( "Connected" );
    }
}

static void disconnected ( struct bt_conn *conn, uint8_t reason )
{
    LOG_INF ( "Disconnected (reason 0x%02x)", reason );
}

BT_CONN_CB_DEFINE ( conn_callbacks )
    = { .connected = connected, .disconnected = disconnected };

K_SEM_DEFINE ( rs485_sem, 0, 1 );
K_CONDVAR_DEFINE ( txDoneVar );
K_CONDVAR_DEFINE ( rxDoneVar );
K_MUTEX_DEFINE ( mutex );
static const struct gpio_dt_spec led = GPIO_DT_SPEC_GET ( LED0_NODE, gpios );
static const struct gpio_dt_spec rs485de
    = GPIO_DT_SPEC_GET ( RS485DE_NODE, gpios );
static const struct gpio_dt_spec cptRst
    = GPIO_DT_SPEC_GET ( CPT_RST_NODE, gpios );
static const struct device *uart = DEVICE_DT_GET ( DT_NODELABEL ( uart1 ) );
static const struct gpio_dt_spec addInc = GPIO_DT_SPEC_GET ( BUT1_NODE, gpios );
static const struct gpio_dt_spec subInc = GPIO_DT_SPEC_GET ( BUT3_NODE, gpios );
static const struct gpio_dt_spec addRes = GPIO_DT_SPEC_GET ( BUT2_NODE, gpios );
static const struct gpio_dt_spec subRes = GPIO_DT_SPEC_GET ( BUT4_NODE, gpios );
static const struct device *rtc2_dev = DEVICE_DT_GET ( DT_NODELABEL ( rtc2 ) );
struct counter_alarm_cfg alarmCfg;
static struct gpio_callback addIncCbData;
static struct gpio_callback subIncCbData;
static struct gpio_callback addResCbData;
static struct gpio_callback subResCbData;
static uint8_t rx_buf_1 [RX_BUFF_SIZE] = { 0 };
static uint8_t rx_buf_2 [RX_BUFF_SIZE] = { 0 };
static uint8_t rx_buf_num = 1;
static uint8_t tx_buf [TX_BUFF_SIZE] = { 0 };

int send_cmd ( cmd_msg_data_t cmd )
{
#if defined( CONFIG_BOARD_NRF52840DK_NRF52840 ) \
    || defined( CONFIG_BOARD_NRF52840DONGLE_NRF52840 )
    return;
#endif

    // Check the semaphore isn't taken
    k_mutex_lock ( &mutex, K_FOREVER );
    if ( k_sem_take ( &rs485_sem, SEM_TIMEOUT ) ) {
        LOG_WRN ( "Failed to get rs485 semaphore!  Transmitting anyways..." );
    }

    // Send the message
    gpio_pin_set_dt ( &rs485de, 1 );
    k_msleep ( 5 );  // Give transciever time to update
    if ( uart_tx ( uart, tx_buf, create_msg ( tx_buf, cmd ), TX_TIMEOUT_US ) ) {
        gpio_pin_set_dt ( &rs485de, 0 );
        k_sem_give ( &rs485_sem );
        LOG_ERR ( "Failed to send message..." );
        return -1;
    }

    // Wait for send
    if ( k_condvar_wait ( &txDoneVar, &mutex, SEM_TIMEOUT ) ) {
        LOG_ERR ( "Timed out waiting for TX done." );
        return -2;
    }
    k_mutex_unlock ( &mutex );

    // Wait for reply
    if ( k_condvar_wait ( &rxDoneVar, &mutex, SEM_TIMEOUT ) ) {
        LOG_ERR ( "Timed out waiting for reply." );
        return -3;
    }
    k_mutex_unlock ( &mutex );

    return 0;
}

static void counter_interrupt_cb ( const struct device *counter_dev,
                                   uint8_t chan_id,
                                   uint32_t ticks,
                                   void *user_data )
{
    buttonStatus_t adj;
    uint64_t delay_us;
    if ( chan_id == INC_ALARM_ID ) {
        adj = evaluateButton ( gpio_pin_get ( addInc.port, addInc.pin ),
                               gpio_pin_get ( subInc.port, subInc.pin ) );
        if ( adj == NOTHING ) {
            return;
        }
        adjustIncline ( adj );
        delay_us = INC_BUTTON_DLY_US;
    } else if ( chan_id == RES_ALARM_ID ) {
        adj = evaluateButton ( gpio_pin_get ( addRes.port, addRes.pin ),
                               gpio_pin_get ( subRes.port, subRes.pin ) );
        if ( adj == NOTHING ) {
            return;
        }
        adjustResistance ( adj );
        delay_us = RES_BUTTON_DLY_US;
    } else {
        LOG_ERR ( "Invalid channel id: %d!", chan_id );
        return;
    }

    // Restart
    alarmCfg.ticks = counter_us_to_ticks ( rtc2_dev, delay_us );
    int err = counter_set_channel_alarm ( counter_dev, chan_id, &alarmCfg );
    if ( err ) {
        LOG_ERR ( "Alarm %d could not be set! Error: %d", chan_id, err );
    }
}

static void incPressed ( const struct device *dev,
                         struct gpio_callback *cb,
                         uint32_t pins )
{
    alarmCfg.ticks = counter_us_to_ticks ( rtc2_dev, INC_BUTTON_DLY_US );
    int err = counter_set_channel_alarm ( rtc2_dev, INC_ALARM_ID, &alarmCfg );
    if ( err ) {
        LOG_ERR ( "Alarm %d could not be set! Error: %d", INC_ALARM_ID, err );
    } else {
        // Setting counter fails if its already been set, which is often the
        // case when there is bounce in the signal.  So only increment if
        // setting the timer does not fail, this implements a psuedo-debounce.
        buttonStatus_t adj
            = evaluateButton ( gpio_pin_get ( addInc.port, addInc.pin ),
                               gpio_pin_get ( subInc.port, subInc.pin ) );
        adjustIncline ( adj );
    }
}

static void resPressed ( const struct device *dev,
                         struct gpio_callback *cb,
                         uint32_t pins )
{
    alarmCfg.ticks = counter_us_to_ticks ( rtc2_dev, RES_BUTTON_DLY_US );
    int err = counter_set_channel_alarm ( rtc2_dev, RES_ALARM_ID, &alarmCfg );
    if ( err ) {
        LOG_ERR ( "Alarm %d could not be set! Error: %d", RES_ALARM_ID, err );
    } else {
        // Setting counter fails if its already been set, which is often the
        // case when there is bounce in the signal.  So only increment if
        // setting the timer does not fail, this implements a psuedo-debounce.
        buttonStatus_t adj
            = evaluateButton ( gpio_pin_get ( addRes.port, addRes.pin ),
                               gpio_pin_get ( subRes.port, subRes.pin ) );
        adjustResistance ( adj );
    }
}

static void add_rx_bytes ( char *buff, size_t offset, size_t len )
{
    static char msg [2 * RX_BUFF_SIZE] = { 0 };
    static size_t pos = 0;
    for ( int i = 0; i < len; i++ ) {
        if ( pos + i >= 2 * RX_BUFF_SIZE ) {
            LOG_ERR ( "Message buffer overflow!" );
            pos = 0;
            memset ( msg, 0, 2 * RX_BUFF_SIZE );
            return;
        }
        msg [pos] = buff [offset + i];
        if ( msg [pos] == TERM_CHAR_8 ) {
            char *start = strrchr ( msg, START_CHAR_8 );
            if ( start ) {
                if ( start != msg ) {
                    LOG_WRN ( "Data thrown out!" );
                }
                int res = new_msg ( start, pos - ( start - msg ) );
                if ( res ) {
                    LOG_ERR ( "Failed to process new message: %d", res );
                }
                k_sem_give ( &rs485_sem );
                k_condvar_signal ( &rxDoneVar );
            }
            pos = 0;
            memset ( msg, 0, 2 * RX_BUFF_SIZE );
        } else {
            pos++;
        }
    }
}

static int enable_rx()
{
    if ( rx_buf_num == 2 ) {
        rx_buf_num = 1;
        return uart_rx_enable ( uart, rx_buf_1, RX_BUFF_SIZE, RX_TIMEOUT_US );
    }
    rx_buf_num = 2;
    return uart_rx_enable ( uart, rx_buf_2, RX_BUFF_SIZE, RX_TIMEOUT_US );
}

static int switch_rx_buf()
{
    if ( rx_buf_num == 2 ) {
        rx_buf_num = 1;
        return uart_rx_buf_rsp ( uart, rx_buf_1, RX_BUFF_SIZE );
    }
    rx_buf_num = 2;
    return uart_rx_buf_rsp ( uart, rx_buf_2, RX_BUFF_SIZE );
}

static void release_rx_buf()
{
    if ( rx_buf_num == 2 ) {
        memset ( rx_buf_1, 0, RX_BUFF_SIZE );
    }
    memset ( rx_buf_2, 0, RX_BUFF_SIZE );
}

static void uart_cb ( const struct device *dev,
                      struct uart_event *evt,
                      void *user_data )
{
    switch ( evt->type ) {
        case UART_TX_DONE:
            memset ( tx_buf, 0, TX_BUFF_SIZE );
            k_msleep ( 2 );
            gpio_pin_set_dt ( &rs485de, 0 );
            k_condvar_signal ( &txDoneVar );
            break;
        case UART_RX_RDY:
            add_rx_bytes ( evt->data.rx.buf,
                           evt->data.rx.offset,
                           evt->data.rx.len );
            break;
        case UART_RX_DISABLED:
            LOG_WRN ( "UART_RX_DISABLED" );
            enable_rx();
            break;
        case UART_TX_ABORTED:
            LOG_WRN ( "UART_TX_ABORTED" );
            gpio_pin_set_dt ( &rs485de, 0 );
            memset ( tx_buf, 0, TX_BUFF_SIZE );
            break;
        case UART_RX_BUF_REQUEST:
            switch_rx_buf();
            break;
        case UART_RX_BUF_RELEASED:
            release_rx_buf();
            break;
        case UART_RX_STOPPED:
            LOG_WRN ( "UART_RX_STOPPED" );
            break;
    }
}

void main ( void )
{
    LOG_INF ( "Starting application, board: %s", CONFIG_BOARD );
    LOG_INF ( "Software: %s:%s", GIT_BRANCH, GIT_COMMIT_HASH );

    LOG_INF ( "Registering callbacks..." );
    setSendMsgCb ( send_cmd );
    ftmsSetTargetsCb ( updateBikeTgts );
    // fecSetTargetsCb ( updateBikeTgts );

    LOG_INF ( "Configuring GPIO..." );
    int ret = 0;
    if ( !device_is_ready ( led.port ) ) {
        ret++;
    }
    if ( !device_is_ready ( rs485de.port ) ) {
        ret++;
    }
    if ( !device_is_ready ( cptRst.port ) ) {
        ret++;
    }
    if ( !device_is_ready ( addInc.port ) ) {
        ret++;
    }
    if ( !device_is_ready ( subInc.port ) ) {
        ret++;
    }
    if ( !device_is_ready ( addRes.port ) ) {
        ret++;
    }
    if ( !device_is_ready ( subRes.port ) ) {
        ret++;
    }
    if ( ret ) {
        LOG_ERR ( "A port was not ready!" );
        return;
    }
    if ( gpio_pin_configure_dt ( &led, GPIO_OUTPUT_ACTIVE ) < 0 ) {
        ret++;
    }
    if ( gpio_pin_configure_dt ( &rs485de, GPIO_OUTPUT_INACTIVE ) < 0 ) {
        ret++;
    }
    if ( gpio_pin_configure_dt ( &cptRst, GPIO_OUTPUT_INACTIVE ) < 0 ) {
        ret++;
    }
    if ( gpio_pin_configure_dt ( &addInc, GPIO_INPUT ) < 0 ) {
        ret++;
    }
    if ( gpio_pin_configure_dt ( &subInc, GPIO_INPUT ) < 0 ) {
        ret++;
    }
    if ( gpio_pin_configure_dt ( &addRes, GPIO_INPUT ) < 0 ) {
        ret++;
    }
    if ( gpio_pin_configure_dt ( &subRes, GPIO_INPUT ) < 0 ) {
        ret++;
    }
    if ( ret ) {
        LOG_ERR ( "Configuration failed of %d devices!", ret );
        return;
    }
    if ( gpio_pin_interrupt_configure_dt ( &addInc, GPIO_INT_EDGE_TO_ACTIVE )
         != 0 ) {
        ret++;
    }
    if ( gpio_pin_interrupt_configure_dt ( &subInc, GPIO_INT_EDGE_TO_ACTIVE )
         != 0 ) {
        ret++;
    }
    if ( gpio_pin_interrupt_configure_dt ( &addRes, GPIO_INT_EDGE_TO_ACTIVE )
         != 0 ) {
        ret++;
    }
    if ( gpio_pin_interrupt_configure_dt ( &subRes, GPIO_INT_EDGE_TO_ACTIVE )
         != 0 ) {
        ret++;
    }
    if ( ret ) {
        LOG_ERR ( "Setting of pin interrupt failed on %d devices!", ret );
        return;
    }
    gpio_init_callback ( &addIncCbData, incPressed, BIT ( addInc.pin ) );
    gpio_init_callback ( &subIncCbData, incPressed, BIT ( subInc.pin ) );
    gpio_init_callback ( &addResCbData, resPressed, BIT ( addRes.pin ) );
    gpio_init_callback ( &subResCbData, resPressed, BIT ( subRes.pin ) );
    if ( gpio_add_callback ( addInc.port, &addIncCbData ) != 0 ) {
        ret++;
    }
    if ( gpio_add_callback ( subInc.port, &subIncCbData ) != 0 ) {
        ret++;
    }
    if ( gpio_add_callback ( addRes.port, &addResCbData ) != 0 ) {
        ret++;
    }
    if ( gpio_add_callback ( subRes.port, &subResCbData ) != 0 ) {
        ret++;
    }
    if ( ret ) {
        LOG_ERR ( "Setting of input callbacks failed on %d devices!", ret );
        return;
    }

    LOG_INF ( "Starting Uart1..." );
    uart = DEVICE_DT_GET ( DT_NODELABEL ( uart1 ) );
    if ( !device_is_ready ( uart ) ) {
        LOG_ERR ( "Uart1 not ready!" );
        return;
    }
    LOG_INF ( "Checking Uart1 ready..." );
    uint32_t start_ms = k_uptime_get_32();
    do {
        ret = uart_err_check ( uart );
        if ( ret ) {
            uint32_t end_ms = k_uptime_get_32();
            if ( end_ms - start_ms > 2000 ) {
                LOG_ERR ( "UART1 check failed: %d", ret );
                return;
            }
            k_msleep ( 10 );
        }
    } while ( ret );
    const struct uart_config uart_cfg
        = { .baudrate = 38400,
            .parity = UART_CFG_PARITY_NONE,
            .stop_bits = UART_CFG_STOP_BITS_1,
            .data_bits = UART_CFG_DATA_BITS_8,
            .flow_ctrl = UART_CFG_FLOW_CTRL_NONE };
    LOG_INF ( "Configuring Uart1..." );
    ret = uart_configure ( uart, &uart_cfg );
    if ( ret ) {
        LOG_ERR ( "Uart1 configure failure: %d", ret );
        return;
    }
    ret = uart_callback_set ( uart, uart_cb, NULL );
    if ( ret ) {
        LOG_ERR ( "Uart1 callback set failure: %d", ret );
        return;
    }
    ret = enable_rx();
    if ( ret ) {
        LOG_ERR ( "Uart1 rx buffer enable failure: %d", ret );
        return;
    }

    LOG_INF ( "Initializing bluetooth..." );
    smp_bt_register();
    ret = bt_enable ( NULL );
    if ( ret ) {
        LOG_ERR ( "Bluetooth init failed (err %d)", ret );
        return;
    }
    LOG_INF ( "Starting advertising..." );
    adv_start();

    LOG_INF ( "Starting counter..." );
    if ( !device_is_ready ( rtc2_dev ) ) {
        LOG_ERR ( "Counter is not ready!" );
        return;
    }
    if ( counter_start ( rtc2_dev ) ) {
        LOG_ERR ( "Counter failed to start!" );
        return;
    }
    alarmCfg.flags = 0;
    alarmCfg.callback = counter_interrupt_cb;
    alarmCfg.user_data = &alarmCfg;

    // Configure nodes
    LOG_INF ( "Configuring bike nodes..." );
    initBike();

    // Start display last so user knows its ready
    LOG_INF ( "Starting Display..." );
    if ( initDisplay() ) {
        LOG_ERR ( "Display initialization failed!" );
        return;
    }

    LOG_INF ( "Startup complete!  Entering loop..." );
    uint32_t exec_ms;
    bike_data_t bikeData;
    while ( 1 ) {
        // Set start time
        start_ms = k_uptime_get_32();

        // Update bike
        gpio_pin_toggle_dt ( &led );
        updateBike();
        bikeData = getBikeData();
#if defined( CONFIG_BOARD_NRF52840DK_NRF52840 ) \
    || defined( CONFIG_BOARD_NRF52840DONGLE_NRF52840 )
        bikeData.act_rpm = ( sys_rand32_get() % 21 ) + 80;
        bikeData.watts = ( sys_rand32_get() % 101 ) + 200;
#endif

        // Update bluetooth services
        bt_cscs_bike_notify ( bikeData );
        bt_cps_notify ( bikeData );
        bt_ftms_bike_notify ( bikeData );
        // bt_fec_update ( bikeData );
        bt_ftms_status_notify();

        // Update display
        updateDisplay ( bikeData );

        // Sleep to hit cycle target
        exec_ms = k_uptime_get_32() - start_ms;
        if ( exec_ms < TGT_CYCLE_MS ) {
            k_msleep ( TGT_CYCLE_MS - exec_ms );
        }
    }
}

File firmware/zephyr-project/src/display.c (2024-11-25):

/*
 * Universal Bike Controller
 * Copyright (C) 2022-2023, Greco Engineering Solutions LLC
 *
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
 * You should have received a copy of the GNU General Public License
 * along with this program.  If not, see <http://www.gnu.org/licenses/>.
 */

#include "display.h"

#include <lvgl.h>
#include <zephyr/drivers/display.h>
#include <zephyr/drivers/kscan.h>
#include <zephyr/drivers/pwm.h>
#include <zephyr/kernel.h>
#include <zephyr/logging/log.h>

#include "common.h"
#include "version.h"

#define BL_PWM_NODE DT_ALIAS ( blpwm )
#define PWM_PERIOD PWM_MSEC ( 1U )  // 1 kHz
#define DIM_MS 10000U               // 10s
#define ASLEEP_MS 60000U            // 60s
#define SEM_TIMEOUT K_MSEC ( 50 )

#define STACKSIZE 2048
#define PRIORITY 15

#define SHA_CHAR_LEN 7
#define MAX_VERSION_LEN 64


LOG_MODULE_REGISTER ( display );

K_SEM_DEFINE ( data_sem, 1, 1 );  // Default to taken
static const struct device *display_dev
    = DEVICE_DT_GET ( DT_CHOSEN ( zephyr_display ) );
static const struct pwm_dt_spec blPwm = PWM_DT_SPEC_GET ( BL_PWM_NODE );
static bike_data_t bikeData = {};

static lv_obj_t *rpm_label;
static lv_obj_t *pwr_label;
static lv_obj_t *inc_label;
static lv_obj_t *res_label;
static lv_obj_t *rpm_desc_label;
static lv_obj_t *pwr_desc_label;
static lv_obj_t *inc_desc_label;
static lv_obj_t *res_desc_label;
static lv_obj_t *version_label;
static lv_obj_t *swLabel;
static lv_obj_t *btnLabel;
static lv_obj_t *btn;
static lv_style_t style;
static lv_style_t descStyle;
static lv_style_t shaStyle;
static lv_style_t btnStyle;
static stopwatch_data_t swData;
static char rpmString [4];                 // 999
static char pwrString [5];                 // 9999
static char incString [7];                 // -10.0%
static char resString [3];                 // 99
static char swString [9];                  // 00:00:00
static char versionString [MAX_VERSION_LEN];

void updateBacklight ( bool wakeUp )
{
    static uint32_t lastActive_ms = 0;
    if ( wakeUp ) {
        lastActive_ms = k_uptime_get_32();
    }

    int64_t elapsed_ms = k_uptime_get_32() - lastActive_ms;
    if ( elapsed_ms < 0 ) {
        elapsed_ms += 1LL << 32;
    }

    uint8_t intensity;
    if ( elapsed_ms < DIM_MS ) {
        intensity = 100;
    } else if ( elapsed_ms < ASLEEP_MS ) {
        intensity = 10;
    } else {
        intensity = 5;
    }

    // Set backlight intensity
    pwm_set_dt ( &blPwm,
                 PWM_PERIOD,
                 ( PWM_PERIOD * ( 100 - intensity ) ) / 100 );
}

static void k_callback ( const struct device *dev,
                         uint32_t row,
                         uint32_t col,
                         bool pressed )
{
    ARG_UNUSED ( dev );
    if ( pressed ) {
        LOG_INF ( "row = %u col = %u\n", row, col );
        updateBacklight ( true );

        if ( col >= 410 ) {
            resetTime();
        }
    }
}

void resetTime()
{
    LOG_INF ( "Resetting timer..." );
    memset ( &swData, 0, sizeof ( stopwatch_data_t ) );
}

static void incrementStopwatch ( int64_t elapsed_ms )
{
    if ( elapsed_ms < 0 ) {
        elapsed_ms += 1LL << 32;
    }
    swData.ms += elapsed_ms;
    while ( swData.ms >= 1000 ) {
        swData.secs++;
        swData.ms -= 1000;
    }
    while ( swData.secs >= 60 ) {
        swData.mins++;
        swData.secs -= 60;
    }
    while ( swData.mins >= 60 ) {
        swData.hrs++;
        swData.mins -= 60;
    }
}

static void updateSwString()
{
    if ( swData.hrs < 10 ) {
        sprintf ( &swString [0], "0%u:", swData.hrs );
    } else {
        sprintf ( &swString [0], "%u:", swData.hrs );
    }
    if ( swData.mins < 10 ) {
        sprintf ( &swString [3], "0%u:", swData.mins );
    } else {
        sprintf ( &swString [3], "%u:", swData.mins );
    }
    if ( swData.secs < 10 ) {
        sprintf ( &swString [6], "0%u", swData.secs );
    } else {
        sprintf ( &swString [6], "%u", swData.secs );
    }
}

static void updateRpmString ( uint16_t act_rpm )
{
    sprintf ( &rpmString [0], "%u", act_rpm );
}

static void updatePwrString ( uint16_t watts )
{
    sprintf ( &pwrString [0], "%u", watts );
}

static void updateIncString ( uint16_t tgt_inc )
{
    int16_t per = ( ( int16_t )tgt_inc - 20 ) / 2;
    if ( tgt_inc < 20 ) {
        sprintf ( &incString [0], "-%d.%u%c", -per, tgt_inc % 2 ? 5 : 0, '%' );
    } else {
        sprintf ( &incString [0], "%d.%u%c", per, tgt_inc % 2 ? 5 : 0, '%' );
    }
}

static void updateResString ( uint16_t disp_res )
{
    sprintf ( &resString [0], "%u", disp_res );
}

static void updateLabels ( bike_data_t bikeData )
{
    updateRpmString ( bikeData.act_rpm );
    updatePwrString ( bikeData.watts );
    updateIncString ( bikeData.tgt_inc );
    updateResString ( bikeData.disp_res );
    updateSwString();

    lv_label_set_text_fmt ( rpm_label, "%s", rpmString );
    lv_label_set_text_fmt ( pwr_label, "%s", pwrString );
    lv_label_set_text_fmt ( inc_label, "%s", incString );
    lv_label_set_text_fmt ( res_label, "%s", resString );
    lv_label_set_text_fmt ( swLabel, "%s", swString );
}

static void updateStopwatch ( bool running )
{
    const uint32_t now_ms = k_uptime_get_32();
    if ( swData.running ) {
        incrementStopwatch ( now_ms - swData.last_ms );
    }
    swData.running = running;
    swData.last_ms = now_ms;
}

static void screenCb ( lv_event_t *e )
{
    updateBacklight ( true );
}

static void buttonCb ( lv_event_t *e )
{
    LOG_INF ( "Timer reset button depressed!" );
    resetTime();
}

static void drawButton()
{
    btn = lv_btn_create ( lv_scr_act() );
    lv_obj_add_event_cb ( btn, buttonCb, LV_EVENT_PRESSED, NULL );
    lv_obj_align ( btn, LV_ALIGN_TOP_MID, 0, 410 );
    lv_obj_set_height ( btn, 60 );
    lv_obj_set_width ( btn, 300 );

    btnLabel = lv_label_create ( btn );
    lv_style_init ( &btnStyle );
    lv_style_set_text_font ( &btnStyle, &lv_font_montserrat_24 );
    lv_obj_add_style ( btnLabel, &btnStyle, 0 );
    lv_label_set_text ( btnLabel, "Reset" );
    lv_obj_center ( btnLabel );
}

/*static void sliderCb ( lv_event_t *e )
{
    lv_obj_t *slider = lv_event_get_target ( e );
    LOG_INF ( "Slider value: %d", lv_slider_get_value ( slider ) );
}

static void drawSlider()
{
    lv_obj_t * slider = lv_slider_create(lv_scr_act());
    lv_obj_align ( slider, LV_ALIGN_TOP_MID, 0, 440 );
    lv_obj_add_event_cb(slider, sliderCb, LV_EVENT_VALUE_CHANGED, NULL);
    lv_obj_set_height ( slider, 30 );
    lv_obj_set_width ( slider, 300 );
}*/

void getGitVersionChar(char *buff)
{
    // Use git tag if not empty
    if (GIT_TAG[0] != '\0') {
        strncpy(buff, GIT_TAG, MAX_VERSION_LEN  - 1);
        buff[MAX_VERSION_LEN  - 1] = '\0';
    // Otherwise fall back on SHA
    } else {
        strncpy(buff, GIT_COMMIT_HASH, SHA_CHAR_LEN);
        buff[SHA_CHAR_LEN] = '\0';
    }
}
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

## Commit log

2023-09-25 Initial commit
    Initial starting point w/ v0.3 hardware files, current firmware project,
    and GPL v3 license.
    [fake-data.csv, uBike.FCStd, uBike.kicad_pcb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]
2023-11-19 Reversed to using kscan callback to reset the screen
    [display.c]
2023-11-20 Revert "Reversed to using kscan callback to reset the screen"
    This reverts commit 9253e350cdc0548603a149c64ceb450167267d3a.
    [display.c]
2023-11-21 Added a 7-digit SHA on the screen, reverted kscan revert
    [display.c, main.c]
2023-11-23 Compiles but doesn't run
    [display.c]
2023-12-28 Roughed in
    [external-connections.kicad_sch, uBike.kicad_pcb, uBike.kicad_sch]
2023-12-30 Changed to 2-layer board
    [uBike.kicad_pcb, uBike.kicad_sch]
2023-12-30 Rounded edges, some cleanup to reduce warnings
    [uBike.kicad_pcb]
2023-12-30 Added stitching vias, other fixes
    [uBike.kicad_pcb]
2023-12-31 Schematic cleanup
    [external-connections.kicad_sch, uBike.kicad_pcb, uBike.kicad_sch]
2023-12-31 Finalized for review
    [external-connections.kicad_sch, uBike.kicad_pcb, uBike.kicad_sch]
2024-01-02 Changed 2.2uF cap footprints and a bit more cleanup
    [external-connections.kicad_sch, uBike-BoM.xlsx, uBike.csv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]
2024-01-03 Created v0.4 board from v0.3 files
2024-01-03 Enabled pull-up resistor and removed lcd reset
    [external-connections.kicad_sch]
2024-01-03 Added inline resistors for ESD on inputs, created order T-V26W325984A
    [external-connections.kicad_sch, uBike.csv, uBike.kicad_pcb]
2024-01-07 First attempt at v4 enclosure
    [uBike.kicad_pcb]
2024-01-31 First pass working
    [uBike-v4.stl]
2024-02-03 Moved up pcb 1.5mm
2024-02-03 Closed up USB hole
    [uBike-v4.stl]
2024-02-11 First pass at LM2596 regulator
    [external-connections.kicad_sch, uBike.kicad_pcb]
2024-02-11 Some general cleanup
    [uBike.kicad_pcb]
2024-02-12 Updated BOM
    [uBike-BoM.xlsx, uBike.csv, uBike.kicad_pcb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]
2024-11-13 Updated model
    [uBike-v4.stl, uBike.stl, uBikeBase.stl]
2024-11-14 Added missing screw holes
    [uBike-v4.FCStd, uBike-v4.stl]

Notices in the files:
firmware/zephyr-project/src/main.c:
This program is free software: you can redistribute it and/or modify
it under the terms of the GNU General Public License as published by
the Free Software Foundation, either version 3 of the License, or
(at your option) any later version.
